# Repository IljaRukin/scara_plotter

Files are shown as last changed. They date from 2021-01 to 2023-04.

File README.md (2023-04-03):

# scara_plotter
scara parallel arm robot plotter with ESP8266 and data transfer over wifi

# files
- "send data to ESP" includes code to send data over GET and POST method with iPython-Notebook to Arduino to toggle a LED
- "esp8266_plotter_v1" and "esp8266_plotter_v2" includes the arduino code for version 1 and 2 of the plotter (the only difference are the movement calculations)
- "send plotter data" includes python code to send a path to be drawn. first the svg is converted to .hpgl using incscape. afterwards a iPython-Notebook sends the coordinates in batches of continuous lines. between these batches the pen is moved up.

here are some images:<br>

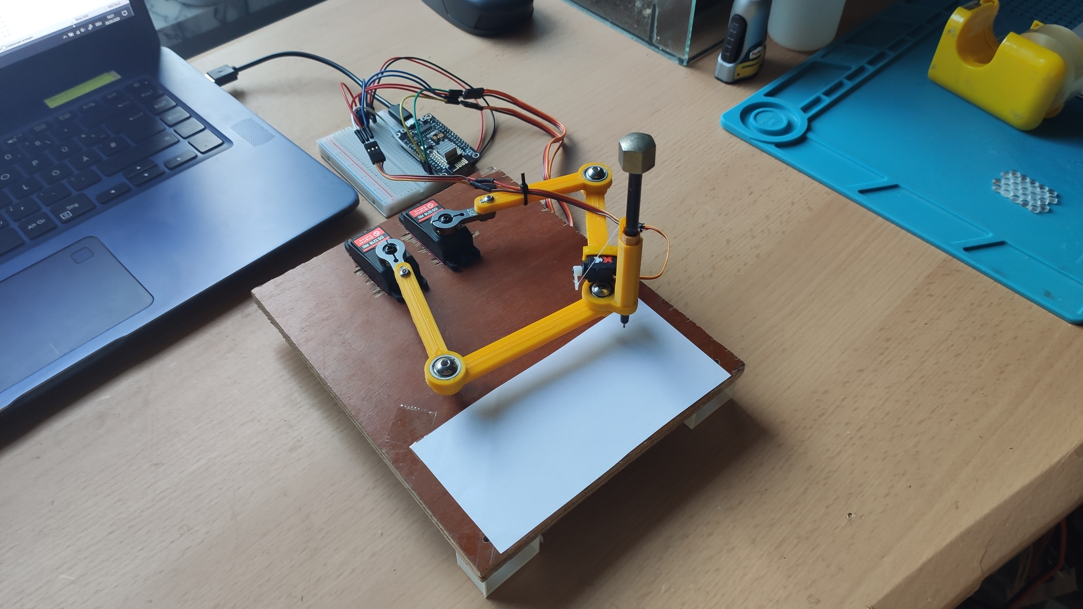
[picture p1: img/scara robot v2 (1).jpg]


and some video links: \
[](https://youtu.be/4elHrwVsAtQ)
[](https://youtu.be/mxgUuI1V4_M)

## version 1
- 2 servos for movement of the two arms and 1 for up/down of whole plattform

### issues
- unstable 
- up/down movement seized often up
- bad pen mount

## version 2
- sturdier construction
- more powerful servos
- improved pen mount and direct up/down control using small servo
- more complex kinematics, since the pen isn't mounted directly on the corner of the parallelogram

### issues
- servo accuracy is quite bad (especially visible when drawing chess board pattern in https://youtu.be/mxgUuI1V4_M)

## kinematics
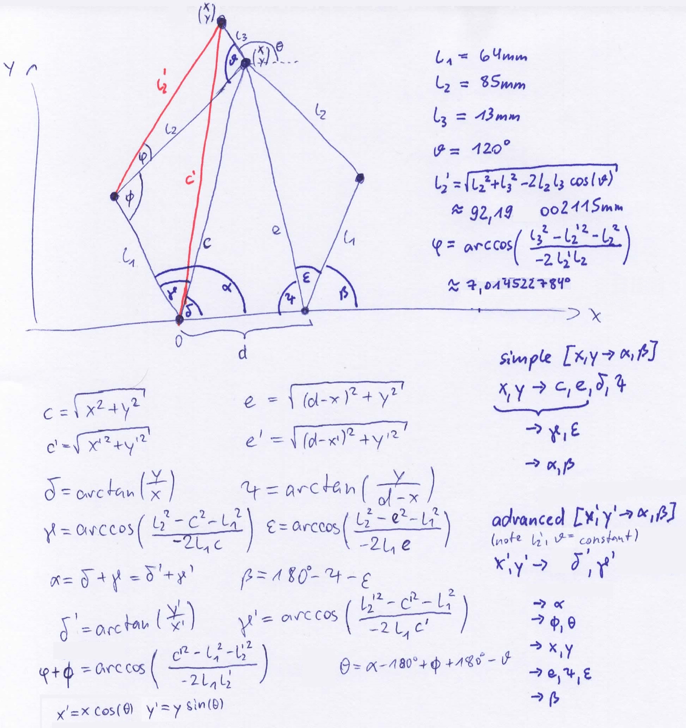
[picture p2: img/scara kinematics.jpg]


the scara robot discribed here operates in "working mode -+". \
note: the bottom image is from: https://www.semanticscholar.org/paper/Development-of-a-Five-Bar-Parallel-Robot-With-Large-Campos-Bourbonnais/4f945b3db879c18c8fdf2b01860d8a9b2f9a274d

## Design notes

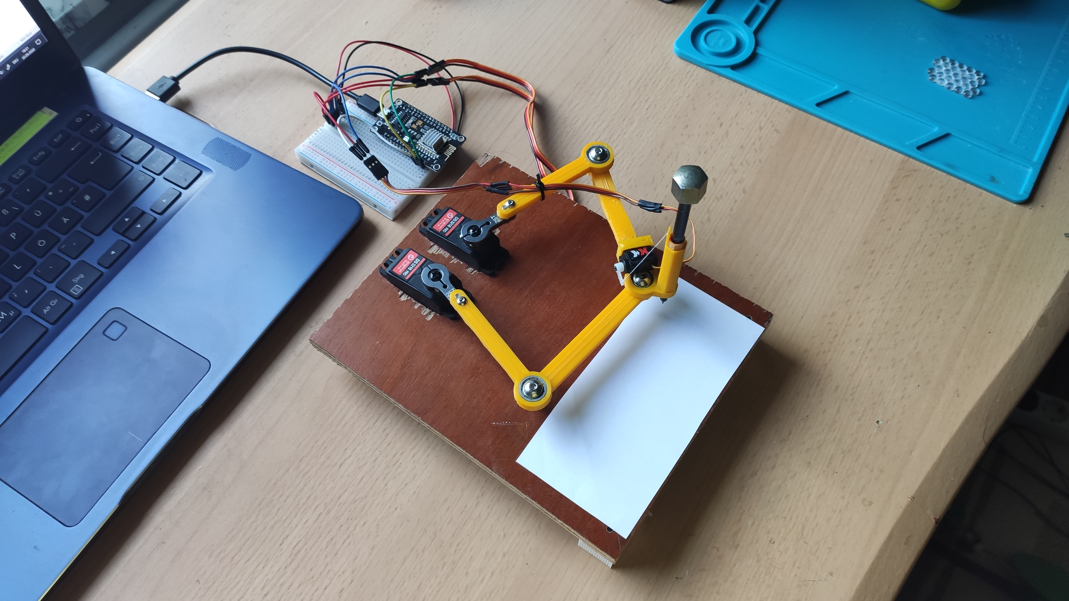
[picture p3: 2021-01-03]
img/scara robot v2 (3).jpg

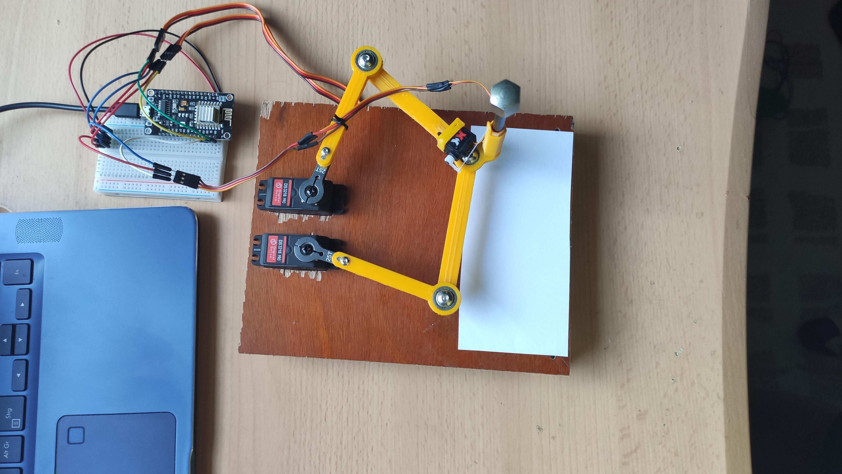
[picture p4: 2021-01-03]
img/scara robot v2 (2).jpg

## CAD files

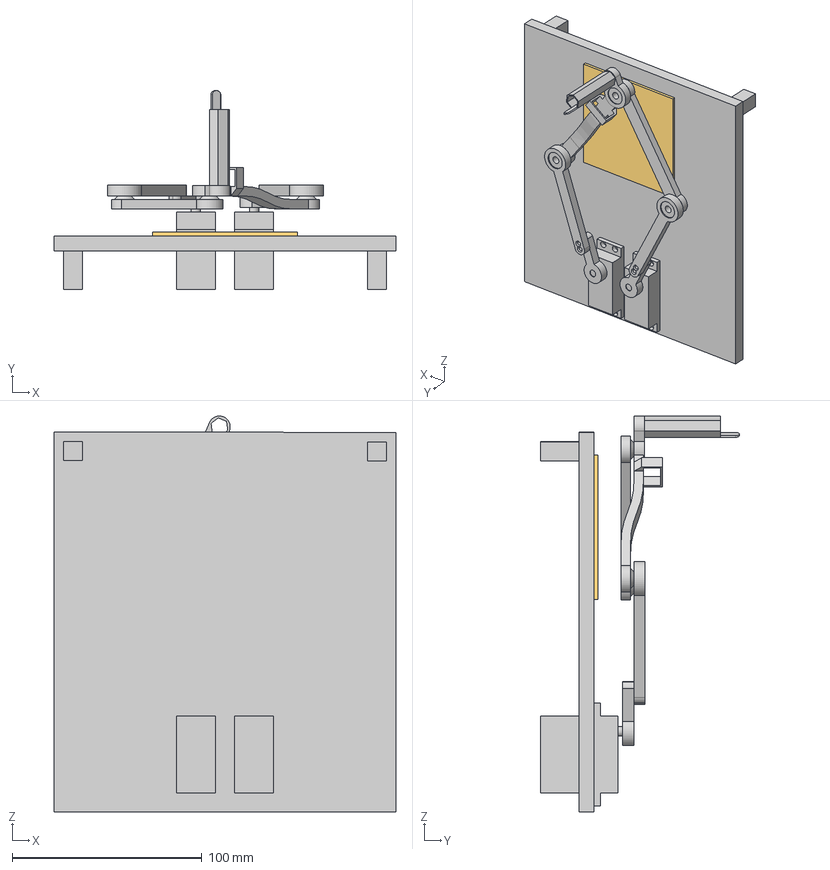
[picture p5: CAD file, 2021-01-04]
3d files/Post it Plotter v2.step
180.1 x 104.8 x 208.6 mm
Post It_1
servo x 2
servo arm x 2
base_1
near arm_2 x 2
bearing_3 x 3
left arm_1
right arm
foot_2 x 2

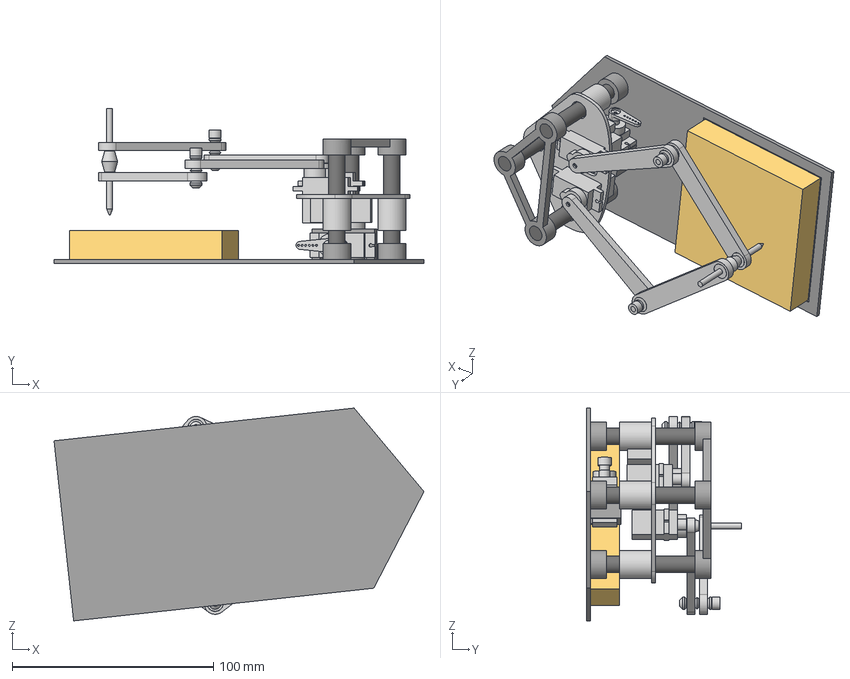
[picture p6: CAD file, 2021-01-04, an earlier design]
3d files/Post it Plotter v1.step
183.8 x 77.2 x 105.7 mm
Post It_1
beam3
beam2
beam1
Top
Base_1
servo
servo (1)
servo (2)
arm (2)
plate
servo arm x 2
bearing 1 x 2
bearing 2 x 2
spacer x 2
spacer (1) x 2
spacer (1) (1) x 2
bolt x 2
nut x 2
arm x 2
bearing 1_1
pen
bearing 2_1
spacer_1

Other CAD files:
3d files/Post it Plotter v1.f3z
3d files/Post it Plotter v1.iges
3d files/Post it Plotter v2.f3z
3d files/Post it Plotter v2.iges

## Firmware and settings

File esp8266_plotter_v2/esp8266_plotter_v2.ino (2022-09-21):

#include "wifi_setup.h"
#include <Servo.h>

#define WIFI_SSID "your_ssid"
#define WIFI_PW "your_pw"

//example received data
//234-34;191-48;157-65;148-71;140-77;131-82;122-88;117-97;

#define PI 3.14159265359
#define Rad2Deg 180/PI
#define Deg2Rad PI/180

//scara parallel arm robot parameters
#define L1 64
#define L2 85
#define L3 13
#define VARTHETA 120*Deg2Rad
//#define L2_ 92.19
#define L2_ sqrt(sq(L2)+sq(L3)-2*L2*L3*cos(VARTHETA))
//#define VARPHI 7.014522784
#define VARPHI acos((-sq(L3)+sq(L2_)+sq(L2))/(2*L2*L2_))
#define D 36
#define X_OFFSET -30
#define Y_OFFSET 105
#define A_OFFSET -4//-4
#define B_OFFSET +6//+3
#define SCALEING 92/90

#define move_delay 50
 
//servo & led
#define LED 2
#define PWM_A D0
#define PWM_B D1
#define PWM_Z D2
#define PEN_UP 50
#define PEN_DOWN 120
Servo servo_a;
Servo servo_b;
Servo servo_z;


void setup(){
  Serial.begin(9600);
  start("KabelBox-E84E","67534404306756752453");
  pinMode(LED,OUTPUT);
  digitalWrite(LED,HIGH);
  servo_a.attach(PWM_A);
  servo_b.attach(PWM_B);
  servo_z.attach(PWM_Z);
  servo_z.write(PEN_UP); //pen up
}

void loop(){
  //init: move to 0
  float x = 0; float y = 0;
  move2(x,y);
  
  while(true){
    //get request
    wait4req = true;
    do{check4req();} while(wait4req == true);
  
    send2client("ack");
  
    //prepare pen
    servo_z.write(PEN_UP); //pen up
  
    //process request
    String data;
    bool process = false; //first find data entry point, than process
    while(client.available()>0){
      digitalWrite(LED,LOW); //led on
      if (process){
        //get one coordinate
        data = client.readStringUntil(';');
        int addr_start = data.indexOf('-');
  
        float next_x = data.substring(0,addr_start).toInt() /10;
        float next_y = data.substring(addr_start + 1).toInt() /10;
        
        Serial.print('x');
        Serial.print(String(next_x));
        Serial.print('-');
        Serial.print('y');
        Serial.print(String(next_y));
        Serial.println(';');
        
        trace_line(next_x,next_y,x,y);
        x = next_x;
        y = next_y;
      }
      else{
        data = client.readStringUntil('\r');
        //Serial.println(data);
        //if (data.indexOf("Connection: close")>0){
        if (data == "\nConnection: close"){
        Serial.println("data: ");
        process = true;
        }
      }
    }
    servo_z.write(PEN_UP); //pen up
    digitalWrite(LED,HIGH); //led off
  }
}

void trace_line(float next_x, float next_y, float x, float y){
  //interpolate between current and next coordinates (bresensham line algorithm) and execute function move2() on every step
  //the algorithm steps along the long side and correct the shorter side if the acculuator "over" reaches a certain value
 
  //go to initial position and move pen down (before tracing):
  move2(x,y);
  delay(move_delay);
  servo_z.write(PEN_DOWN); //pen down
  
  long i = 0; //steps in long direction
  long over; //accumulator
  //distances in x & y
  long dx = next_x - x;
  long dy = next_y - y;
  //directions (positive/negative):
  int dirx = dx>0 ? 1:-1;
  int diry = dy>0 ? 1:-1;
 //distances in x & y without sign
  dx = abs(dx);
  dy = abs(dy);

  //trace
  if(dx>dy){
    over = dx/2;
    for(i=0; i<dx; i++){
      over += dy;
      x += dirx; //take steps in x direction
      if(over>=dx){
        over -= dx;
        y += diry; //add step in y direction
      }
      move2(x,y);
      delay(move_delay);
    }
  }
  else{
    over = dy/2;
    for(i=0; i<dy; i++){
      over += dx;
      y += diry; //take steps in y direction
      if(over>=dy){
        over -= dy;
        x += dirx; //add step in x direction
      }
      move2(x,y);
      delay(move_delay);
    }
  }
  servo_z.write(PEN_DOWN); //pen down
}


void move2(float x_, float y_){
  
  Serial.print(" x_ ");
  Serial.print(String(x_));
  Serial.print(" y_: ");
  Serial.println(String(y_));
  
  x_ += X_OFFSET;
  y_ += Y_OFFSET;
  
  //calculate
  float delta_ = atan2(y_,x_);
  float c_ = sqrt(sq(x_)+sq(y_));
  float gamma_ = acos((-sq(L2_)+sq(c_)+sq(L1))/(2*L1*c_));
  float alpha = delta_ + gamma_;
  float phi = acos((-sq(c_)+sq(L1)+sq(L2_))/(2*L1*L2_)) - VARPHI;
  float theta = alpha + phi - VARTHETA;
  float x = x_+L3*sin(theta-PI/2);
  float y = y_-L3*cos(theta-PI/2);
  float e = sqrt(sq(D-x)+sq(y));
  float psi = atan2(y,(D-x));
  float epsillon = acos((-sq(L2)+sq(e)+sq(L1))/(2*L1*e));
  float beta = (PI - psi - epsillon)*Rad2Deg;
  alpha = alpha*Rad2Deg;
  /*
  Serial.print(" delta_ ");
  Serial.print(String(delta_));
  Serial.print(" c_ ");
  Serial.print(String(c_));
  Serial.print(" gamma_ ");
  Serial.print(String(gamma_));
  Serial.print(" alpha_ ");
  Serial.print(String(alpha));
  Serial.print(" phi ");
  Serial.print(String(phi));
  Serial.print(" theta ");
  Serial.print(String(theta));
  Serial.print(" x ");
  Serial.print(String(x));
  Serial.print(" y ");
  Serial.print(String(y));
  Serial.print(" e ");
  Serial.print(String(e));
  Serial.print(" psi ");
  Serial.print(String(psi));
  Serial.print(" epsilon ");
  Serial.print(String(epsillon));
  Serial.print(" beta ");
  Serial.println(String(beta));
  */
  alpha = alpha +A_OFFSET;
  beta = beta +B_OFFSET;
  
  //move
  servo_a.write((uint8_t)alpha*SCALEING);
  servo_b.write((uint8_t)beta*SCALEING);
}

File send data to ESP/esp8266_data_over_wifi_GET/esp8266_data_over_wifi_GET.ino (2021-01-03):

#include "wifi_setup.h"

#define WIFI_SSID "your_ssid"
#define WIFI_PW "your_pw"
#define LED 2

void do_something(String data){
  //turn LED on/off
  if (data=="/LED_ON"){
    digitalWrite(LED,LOW);
  }
  if (data=="/LED_OFF"){
    digitalWrite(LED,HIGH);
  }
  return;
}

void setup(){
  Serial.begin(9600);
  start(WIFI_SSID,WIFI_PW);
  pinMode(LED,OUTPUT);
}

void loop(){
  //get request
  wait4req = true;
  do{check4req();} while(wait4req == true);

  send2client("ack");

  //process request
  String data;
  int addr_start = req.indexOf(' ');
  int addr_end = req.indexOf(' ', addr_start + 1);
  data = req.substring(addr_start + 1, addr_end);
  Serial.println("data:");
  Serial.println(data);
  
  do_something(data);
}
